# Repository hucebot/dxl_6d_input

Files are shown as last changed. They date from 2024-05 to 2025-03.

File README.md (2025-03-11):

# dxl_6d_input

[](
https://opensource.org/licenses/BSD-3-Clause)
[](
http://wiki.ros.org/noetic)

ROS package for a 6-d input device based on dynamixels.

The end effector of the device is a 6-DOF manipulator with 2 MX-64 and 5 MX-28 Dynamixels. The device is controlled by a ROS node that reads the position of the end effector and publishes it to a topic as also the position of the gripper. The node also subscribes to a topic to receive the actual position of the robot end effector to compensate the initial position of the device.

### Topics
#### Publishers
- `/dxl_6d_input/pos_{side}` - Publishes the position of the end effector.
- `/dxl_6d_input/gripper_{side}` - Publishes the position of the gripper.

#### Subscribers
- `/cartesian/gripper_{side}_grasping_frame/current_reference` - Subscribes to the position of the robot end effector.
- `/streamdeck/teleoperation_mode` - Subscribes to the teleoperation mode of the device.
- `/joy` - Subscribes to the joystick input.

### Parameters
- `~urdf_filename` - The URDF file of the device.
- `~ids` - The IDs of the Dynamixels.
- `~devicename` - The name of the port where the USB2Dynamixel is connected.
- `~baudrate` - The baudrate of the USB2Dynamixel.
- `~protocol_version` - The protocol version of the USB2Dynamixel.
- `~addr_present_position` - The address of the present position register.
- `~len_present_position` - The length of the present position register.
- `~debuginfo` - Flag to enable the debug information.
- `~arm_side` - The side of the arm.
- `~position_topic` - The topic where the position of the robot end effector is published.
- `~gripper_topic` - The topic where the position of the gripper is published.
- `~robot_position_topic` - The topic where the position of the robot end effector is subscribed.
- `~space_scalar` - The scalar to convert the position of the robot end effector to the device.

# Get Started

| 3D Design | 3D Design |
|---|---|
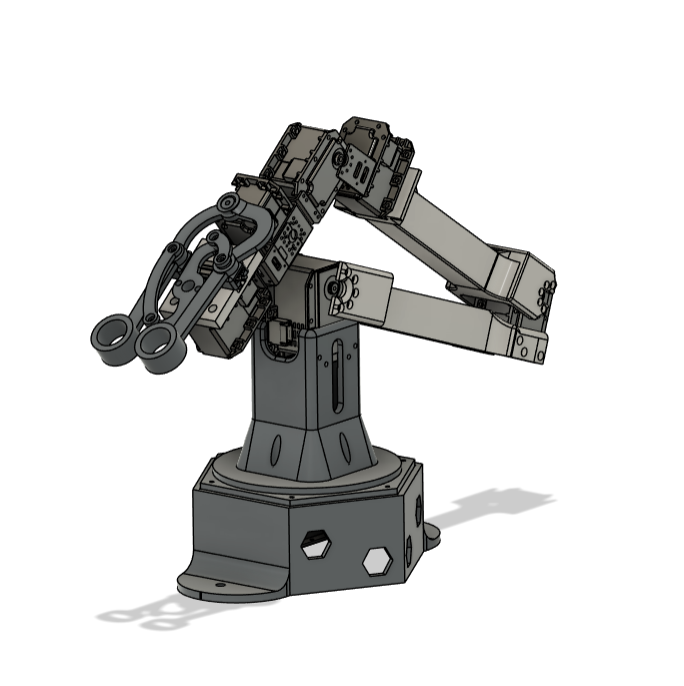
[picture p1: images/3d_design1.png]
3D Design
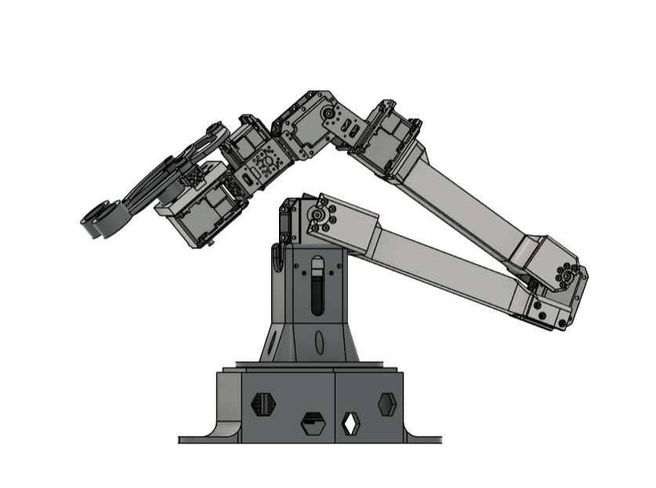
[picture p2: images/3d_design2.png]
3D Design
|  |  |

## Hardware
For the hardware setup, the package is designed to work with the 2 Dynamixel MX-64 and 5 Dynamixel MX-28 actuators. All the 3D parts can be found in the `dxl_6d_input/armd_design` folder where you will find the FreeCad files and the STL files for 3D printing. To assemble the device, you can follow the next steps:

### Shopping List
- 2 Dynamixel MX-64.
- 5 Dynamixel MX-28.
- 2 FR07 - H101K
- 4 FR07 - S101K
- Dynamixel cables.
- 1 USB2Dynamixel.
- 3D printed parts - PLA.
- Screws and nuts (M2, M3, M4, M5).
- 1 aluminum profile (10x10 mm) - 100 mm.

### Assembly
- Print the parts in the `dxl_6d_input/armd_design` folder. All the parts are designed to be printed with a **0.4mm nozzle and 0.2mm** layer height, with **40% infill** and **supports enabled** using **PLA**.
    - The files `finger_1.stl`, `finger_2.stl`, `griper_axis.stl`, `griper_axis_1.stl`, `griper_axis_1.stl` should be mirrored to print the left arm.
    - Once the parts are printed, you can start the assembly.
- The 2 Dynamixel MX-64 should be mounted on the base of the device, while the 5 Dynamixel MX-28 should be mounted on the arm.
- Be aware of the orientation of the Dynamixels:
    - First calibrate each motor to the zero position using the [Dynamixel Wizard2](https://emanual.robotis.com/docs/en/software/dynamixel/dynamixel_wizard2/).
    - Mount each motor following the joints directions. For a beter understanding of the joints, you can check the URDF file in the `dxl_6d_input/src` folder and view it with any URDF viewer.
- The aluminum profile should be mounted as a guide for the gripper. You can see it on the images above.
- We strongly **recommend to assemble from the bottom to the top.**
- For more information about the assembly, check [assembly instructions](https://github.com/hucebot/dxl_6d_input/blob/bimanual-teleoperation/assembly_guide.pdf)

## Installation

### From Docker

The easiest way to get started is to use the provided Docker image. You can find the Dockerfile in the `docker` folder. To build the image, run the following command:

```sh build.sh```

The run the command below to start the container (inside the `docker` folder):

```sh run_docker.sh```

# Usage

## Prepare the Dynamixels

Before starting the node, make sure that the Dynamixels are connected to the computer and that the USB2Dynamixel is connected to the computer. Also check the following:
- The protocol version is set to 2.0 for each Dynamixel.
- The baudrate is set to 1Mbps for each Dynamixel.
- The left arm it's connected to /dev/ttyUSB0 and the right arm to /dev/ttyUSB1.
- The Dynamixels are connected in the following order:

<center>

| Left Arm | Right Arm  |
| ------------- | ------------- |
| MX-64 - ID 1  | MX-64 - ID 11  |
| MX-64 - ID 2  | MX-64 - ID 12  |
| MX-28 - ID 3  | MX-28 - ID 13  |
| MX-28 - ID 4  | MX-28 - ID 14  |
| MX-28 - ID 5  | MX-28 - ID 15  |
| MX-28 - ID 6  | MX-28 - ID 16  |
| MX-28 - ID 7  | MX-28 - ID 17  |

</center>

## Start the Node

Once the Dynamixels are connected, you can start the node running the following command:

```roslaunch dxl_6d_input dxl_6d_input.launch```

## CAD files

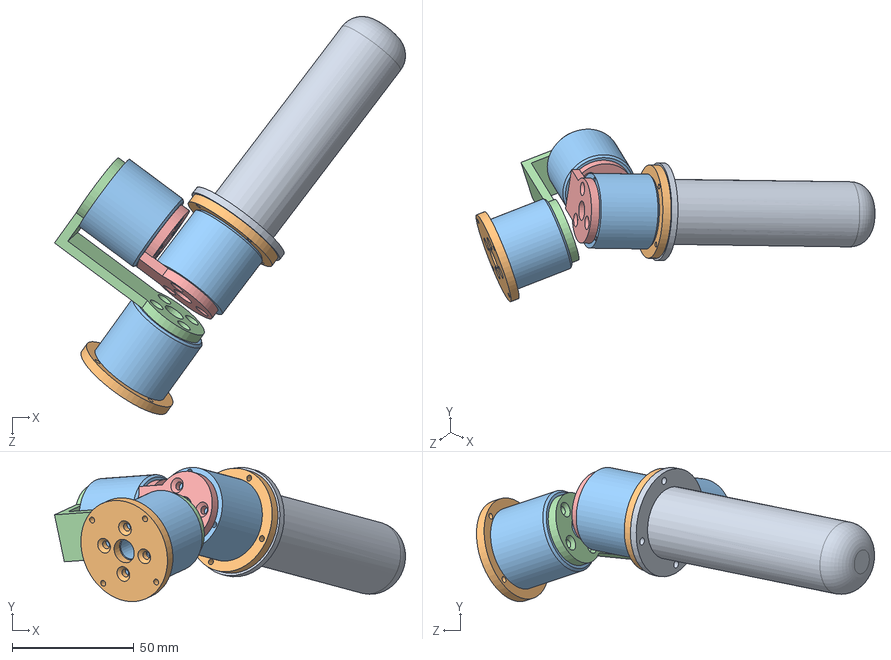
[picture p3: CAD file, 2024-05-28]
hardware/armAssembly.SLDASM
143.9 x 55.0 x 163.2 mm
handle
hub1 x 2
motorgl30 x 3
motorMount1
motorMount2

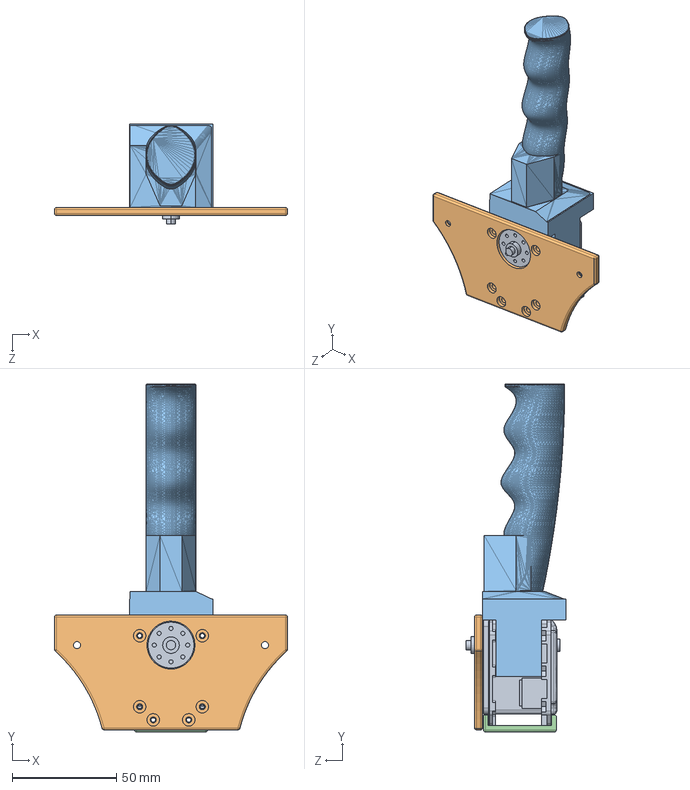
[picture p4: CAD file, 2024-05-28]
hardware/alohaRemixAsmb.SLDASM
111.6 x 166.6 x 48.1 mm
MX-28AT_AR.stp
motorHubDynamixel
handle_lower1_remix
handlerLinkDynamix1

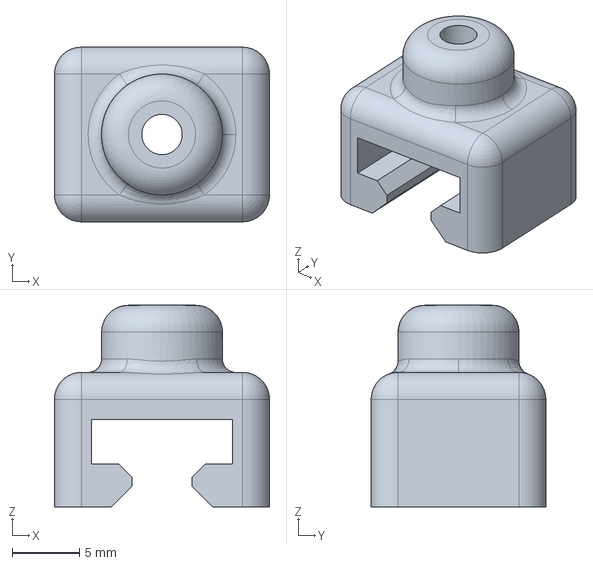
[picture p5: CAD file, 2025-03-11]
arm_design/auxiliar_guide.FCStd
16.0 x 13.0 x 15.0 mm

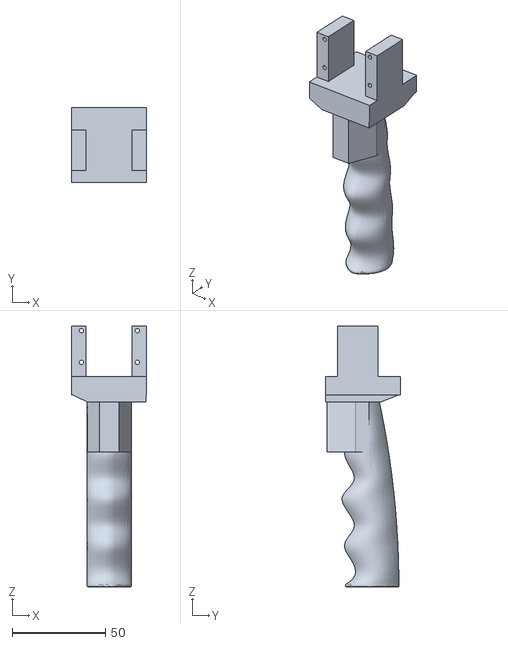
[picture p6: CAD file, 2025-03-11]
arm_design/stl_files/handle.stl
40.0 x 40.0 x 140.0

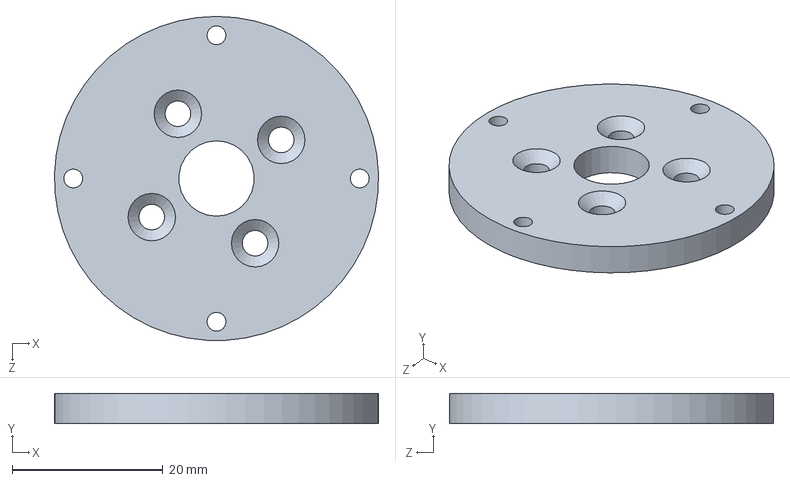
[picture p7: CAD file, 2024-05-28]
hardware/simpleGimball/hub1.SLDPRT
43.0 x 4.00 x 43.0 mm

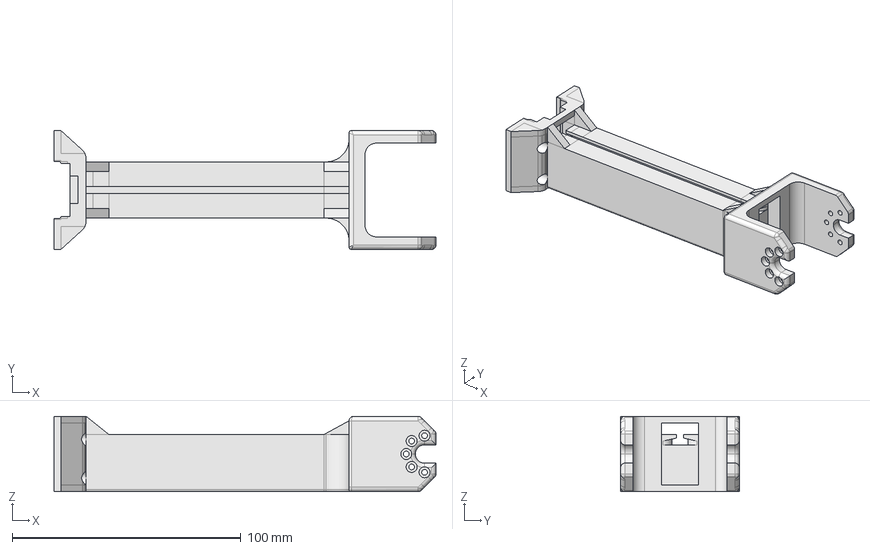
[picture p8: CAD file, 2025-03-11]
arm_design/arm_l2_fixed.FCStd
167.0 x 52.0 x 33.0 mm

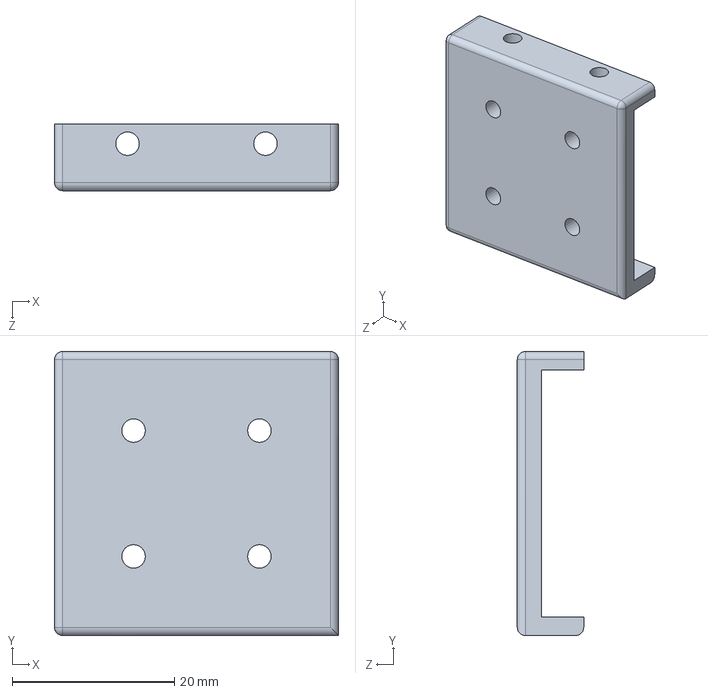
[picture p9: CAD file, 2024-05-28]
hardware/handlerLinkDynamix1.SLDPRT
35.0 x 35.0 x 8.20 mm

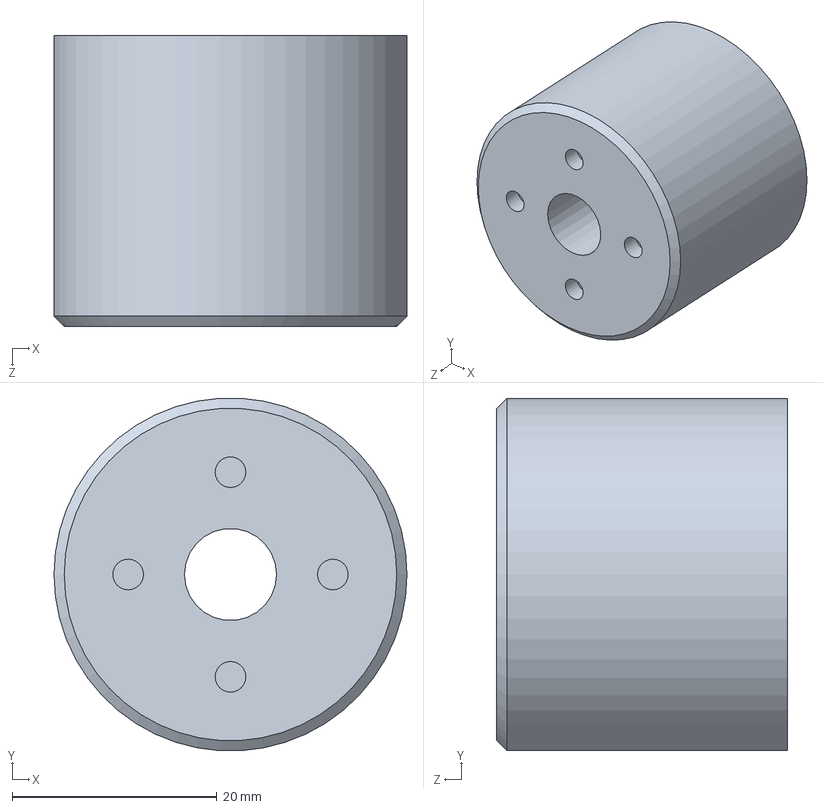
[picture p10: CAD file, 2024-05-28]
hardware/simpleGimball/motorgl30.SLDPRT
34.5 x 34.4 x 28.4 mm

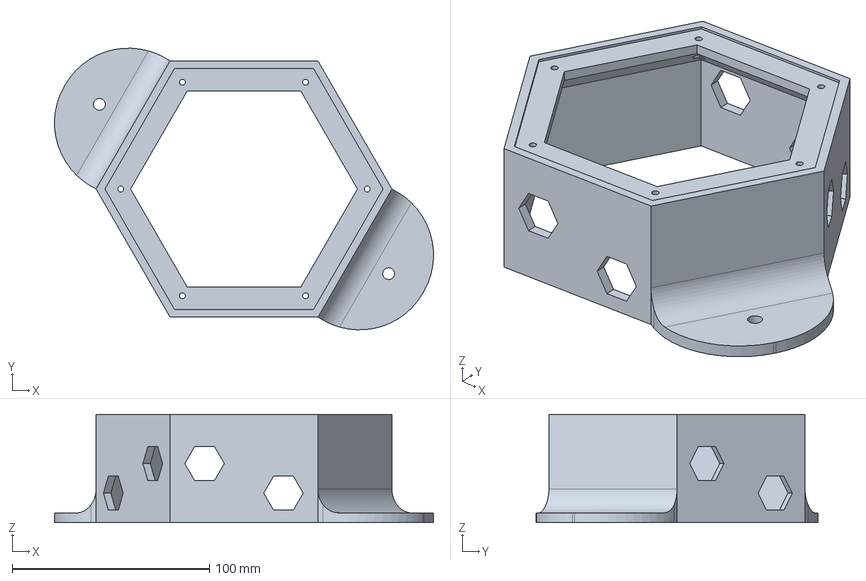
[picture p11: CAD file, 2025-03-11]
arm_design/base_1.FCStd
192.1 x 142.8 x 55.0 mm

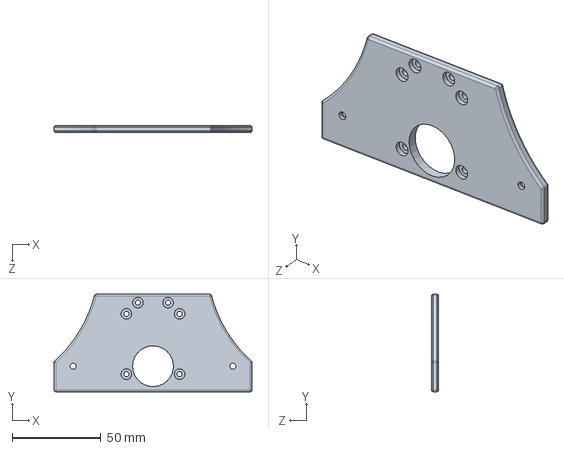
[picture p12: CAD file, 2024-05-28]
hardware/motorHubDynamixel.SLDPRT
111.6 x 55.0 x 4.00 mm

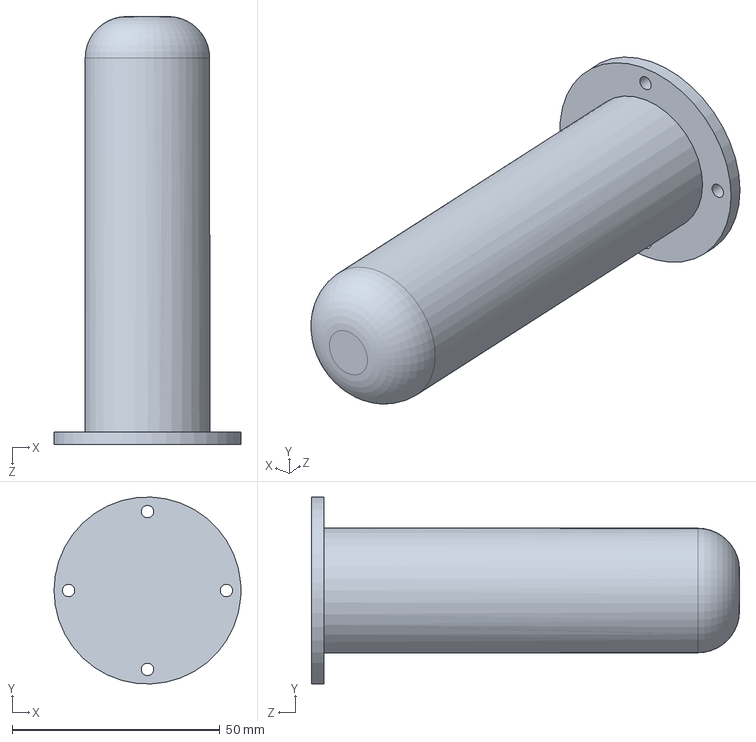
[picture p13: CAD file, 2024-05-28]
hardware/simpleGimball/handle.SLDPRT
45.0 x 45.0 x 103.0 mm

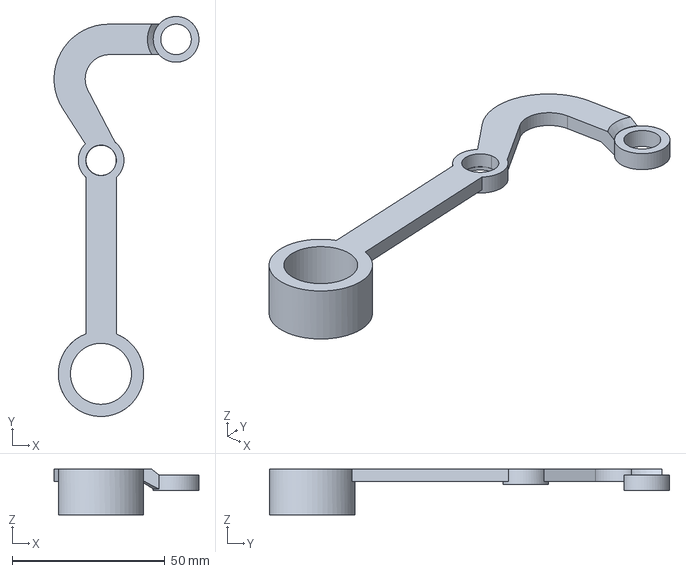
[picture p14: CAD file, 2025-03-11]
arm_design/finger_2.FCStd
47.5 x 131.2 x 15.0 mm

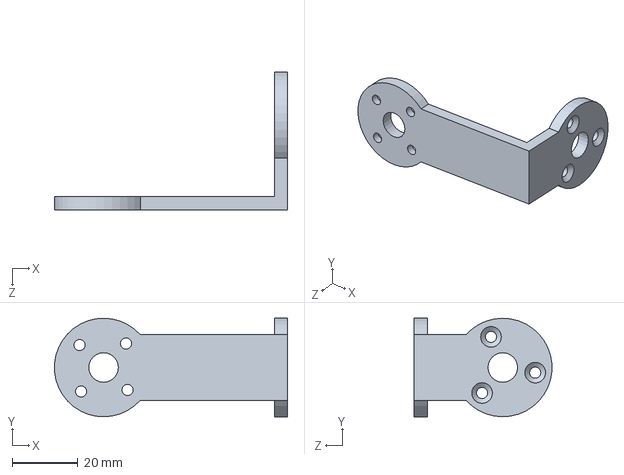
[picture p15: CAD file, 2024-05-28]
hardware/simpleGimball/motorMount1.SLDPRT
70.9 x 30.0 x 41.9 mm

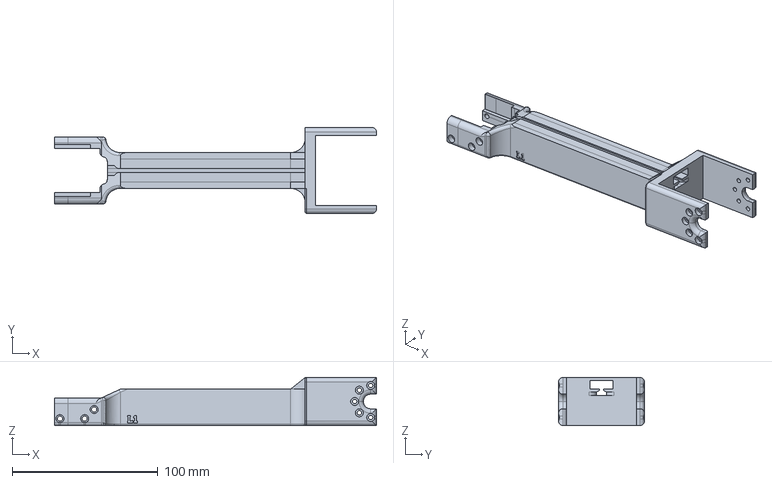
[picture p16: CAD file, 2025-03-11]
arm_design/arm_l1_fixed.FCStd
221.2 x 59.0 x 33.0 mm

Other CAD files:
hardware/simpleGimball/motorMount2.SLDPRT
arm_design/auxiliar_tape.FCStd
arm_design/base.FCStd
arm_design/gripper_motor_mount.FCStd
arm_design/base_0.FCStd
arm_design/base_plate.FCStd
arm_design/finger_1.FCStd
arm_design/gripper_axis.FCStd
arm_design/gripper_axis_1.FCStd
arm_design/gripper_axis_2.FCStd
arm_design/stl_files/arm_l1_fixed.stl
arm_design/stl_files/arm_l2_fixed.stl
arm_design/stl_files/auxiliar_guide.stl
arm_design/stl_files/auxiliar_tape.stl
arm_design/stl_files/base.stl
arm_design/stl_files/base_0.stl
arm_design/stl_files/base_1.stl
arm_design/stl_files/base_plate.stl
arm_design/stl_files/finger_1.stl
arm_design/stl_files/finger_2.stl
arm_design/stl_files/gripper_axis.stl
arm_design/stl_files/gripper_axis_1.stl
arm_design/stl_files/gripper_axis_2.stl
arm_design/stl_files/gripper_motor_mount.stl

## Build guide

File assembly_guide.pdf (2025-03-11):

# DXL 6D INPUT

# Assembly Guide

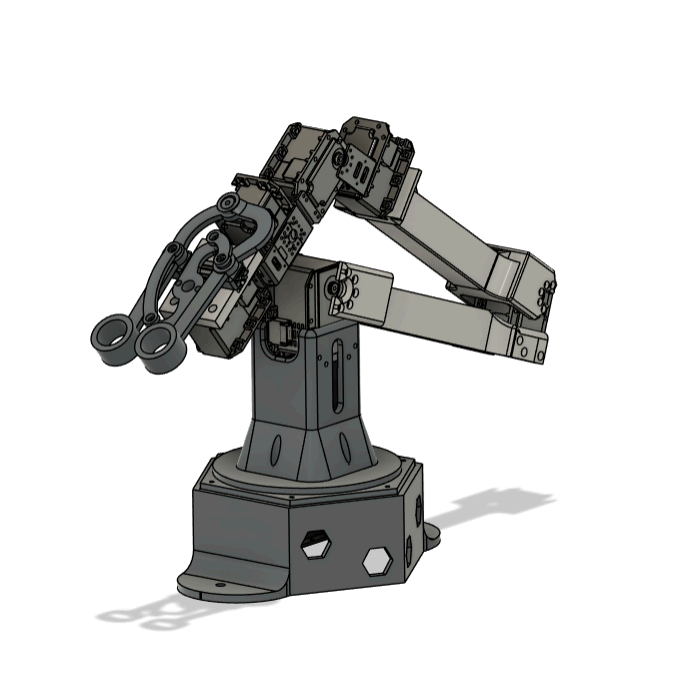
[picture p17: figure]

# Assembly Guide

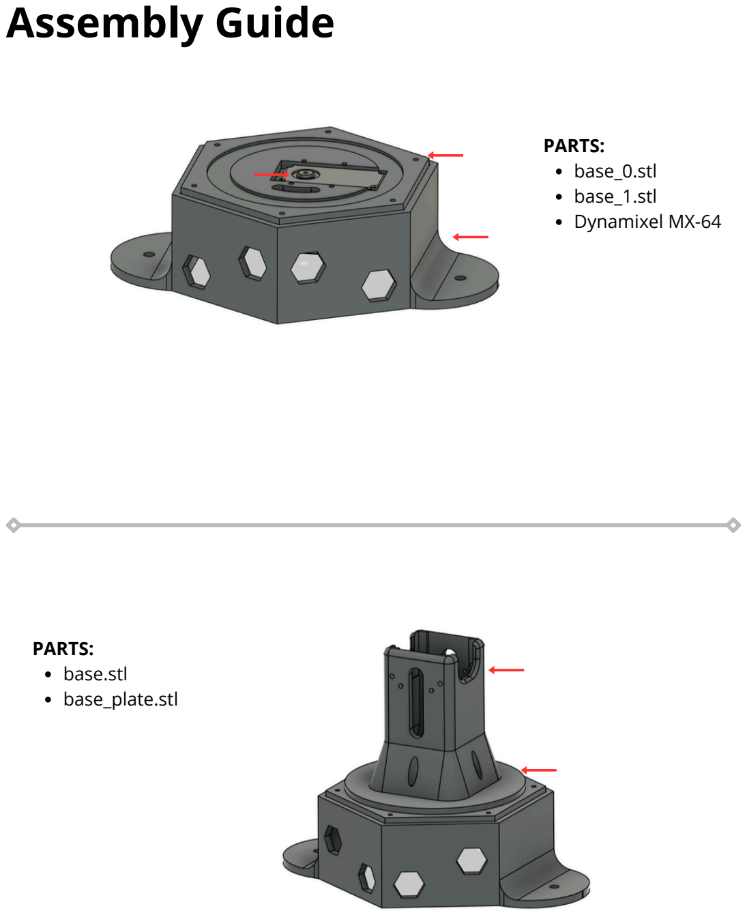
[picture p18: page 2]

PARTS:
base_0.stl
base_1.stl
Dynamixel MX-64

PARTS:
base.stl
base_plate.stl

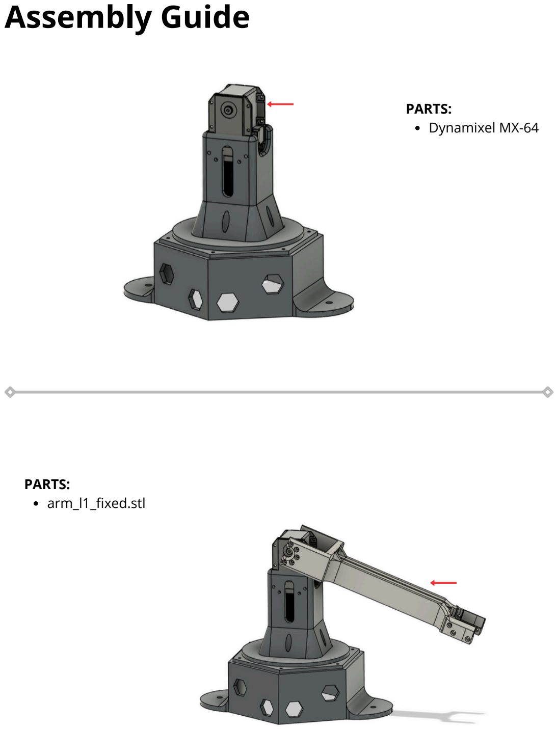
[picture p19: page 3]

PARTS:
Dynamixel MX-64

PARTS:
arm_l1_fixed.stl

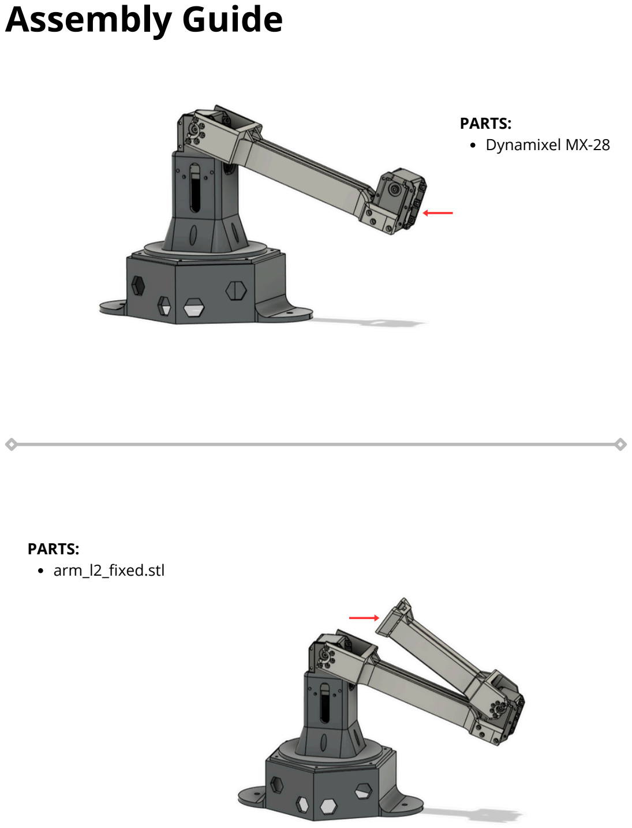
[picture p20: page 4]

PARTS:
Dynamixel MX-28

PARTS:
arm_l2_fixed.stl

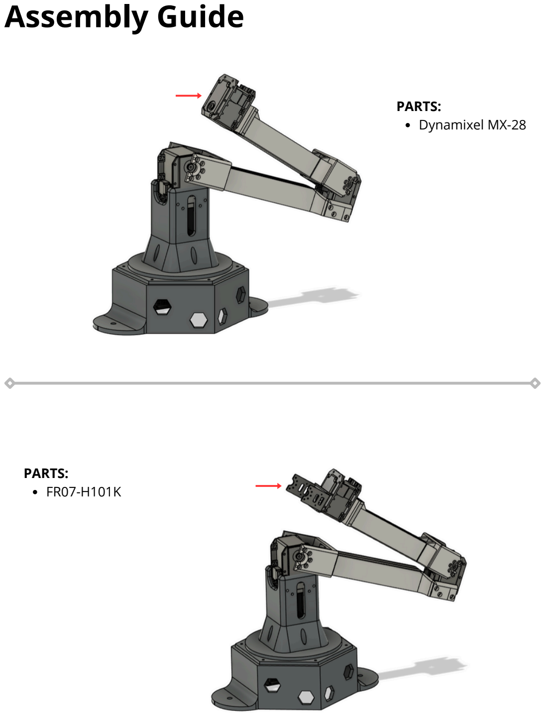
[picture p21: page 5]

PARTS:
Dynamixel MX-28

PARTS:
FR07-H101K

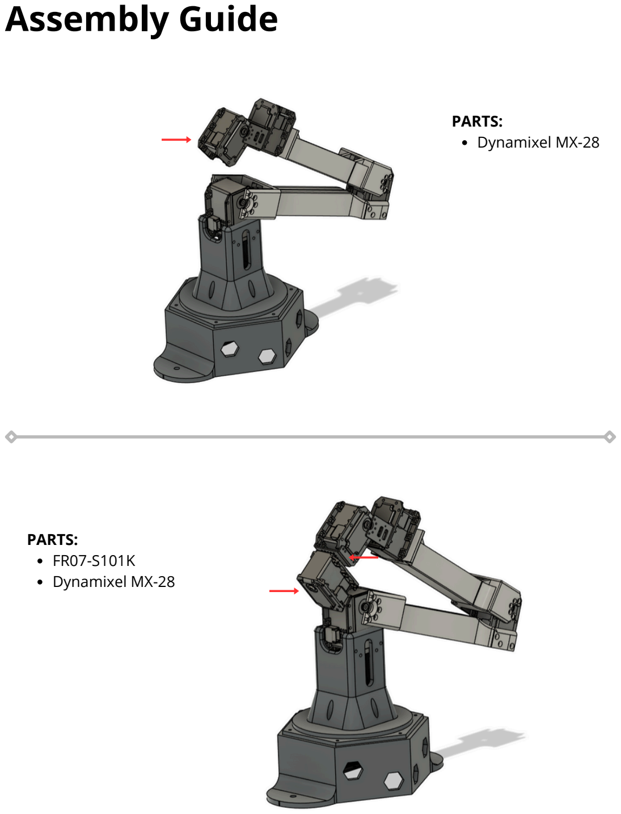
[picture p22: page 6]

PARTS:
Dynamixel MX-28

PARTS:
FR07-S101K
Dynamixel MX-28

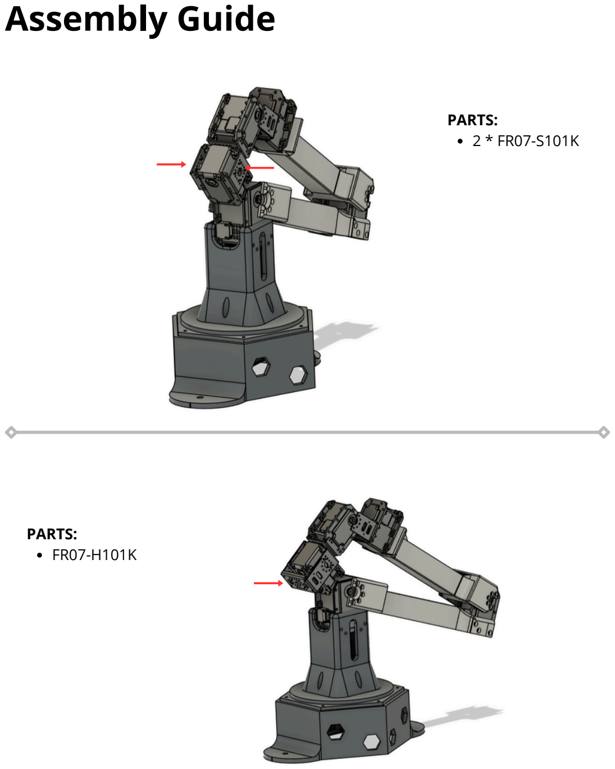
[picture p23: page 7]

PARTS:
2 * FR07-S101K

PARTS:
FR07-H101K

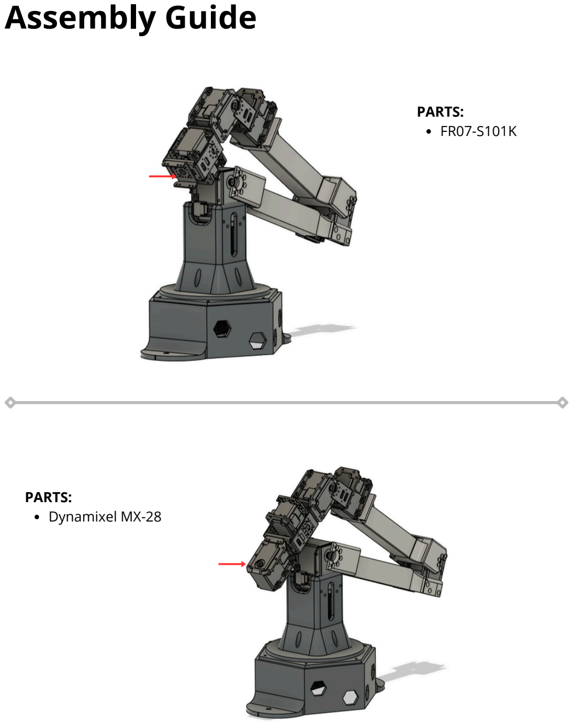
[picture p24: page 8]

PARTS:
FR07-S101K

PARTS:
Dynamixel MX-28

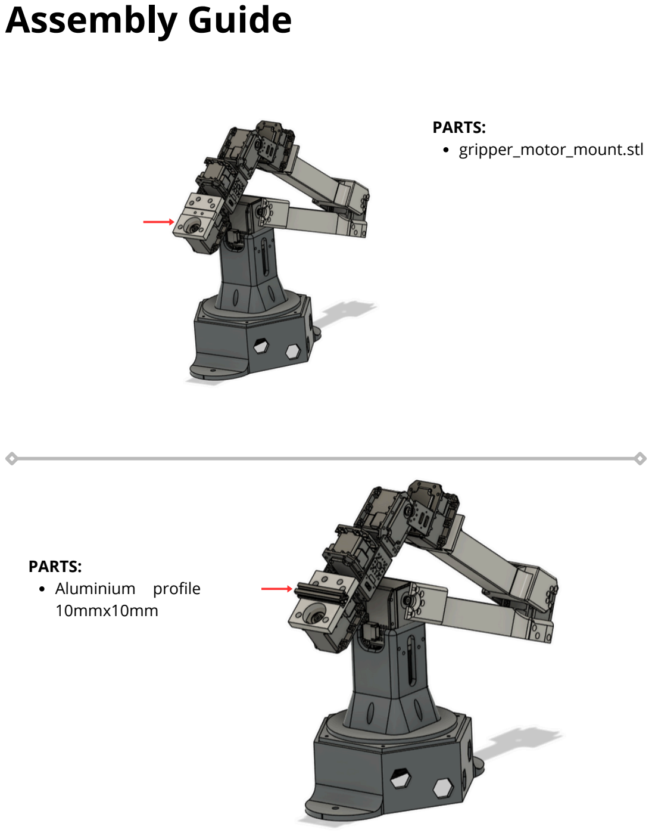
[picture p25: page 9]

PARTS:
gripper_motor_mount.stl

PARTS:
Aluminium profile
10mmx10mm

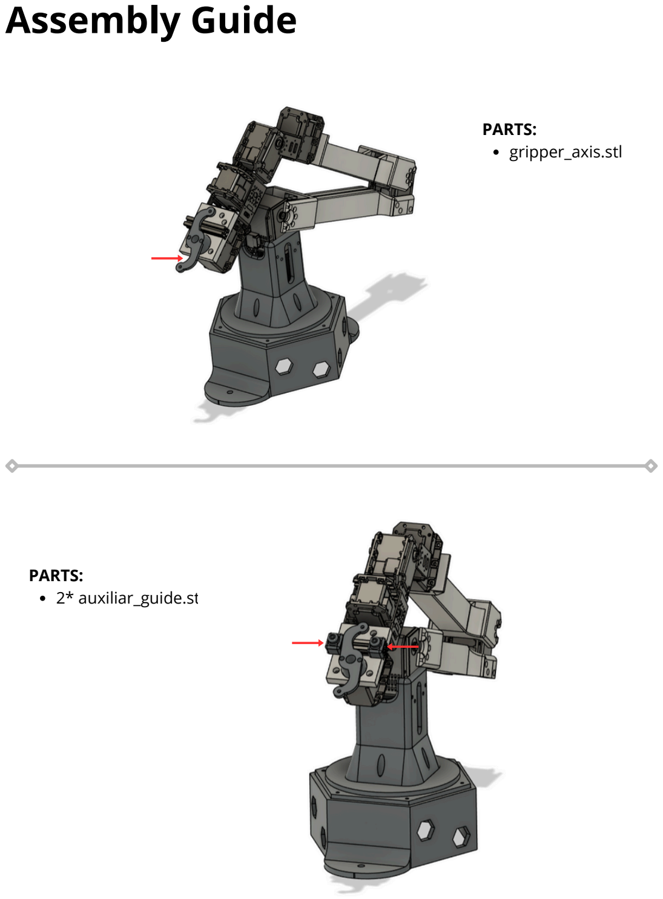
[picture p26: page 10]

PARTS:
gripper_axis.stl

PARTS:
2* auxiliar_guide.stl

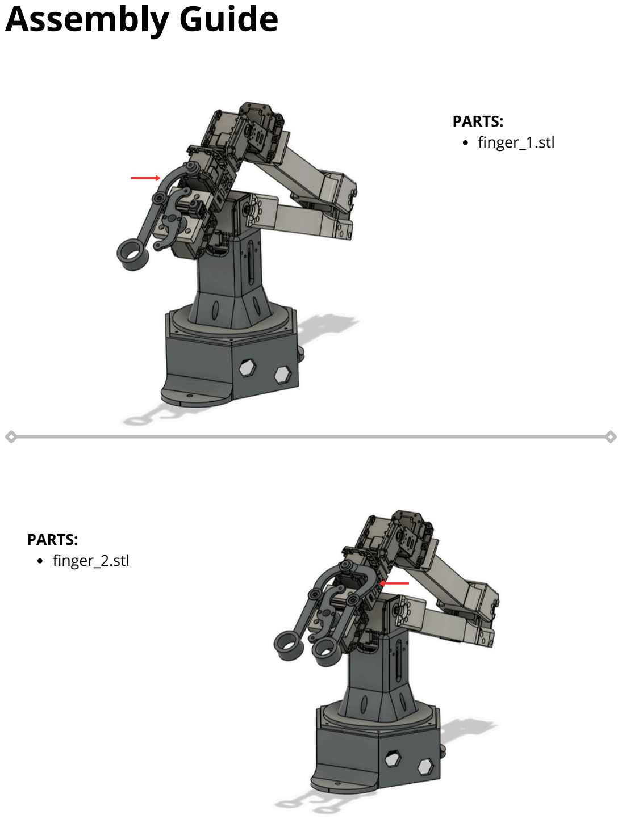
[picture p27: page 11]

PARTS:
finger_1.stl

PARTS:
finger_2.stl

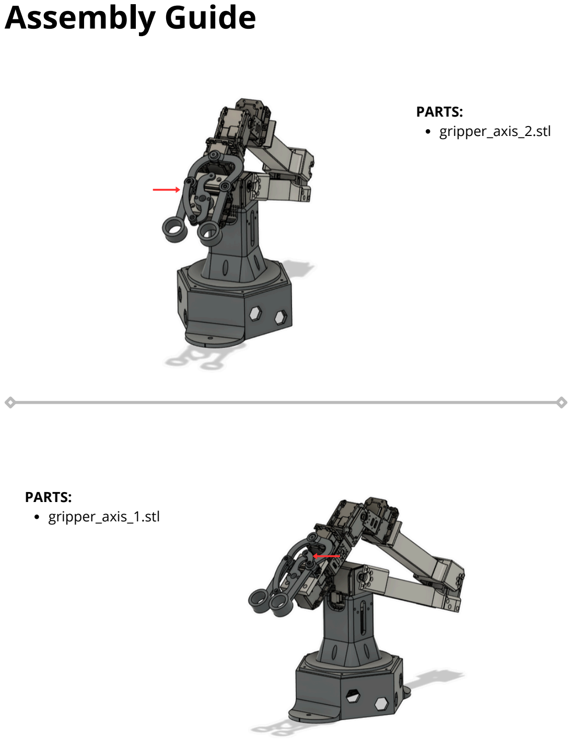
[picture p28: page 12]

PARTS:
gripper_axis_2.stl

PARTS:
gripper_axis_1.stl

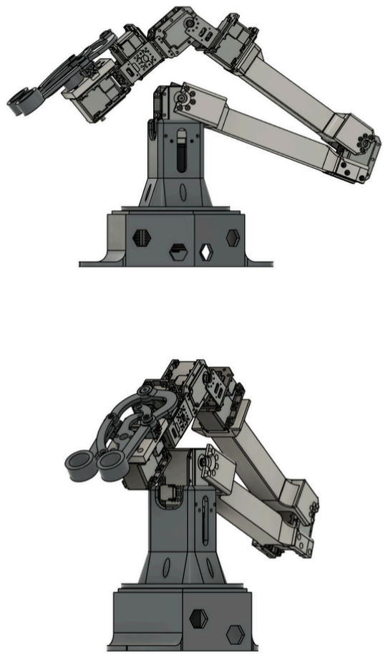
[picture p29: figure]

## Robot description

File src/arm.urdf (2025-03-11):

<?xml version="1.0"?>
<robot name="omnipointer">
  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
  <link name="base_link">
    <inertial>
      <origin rpy="0 0 0" xyz="0 0 0" />
      <mass value="10.0" />
      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
    </inertial>
  </link>
  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
  <joint name="arm_joint_0" type="fixed">
    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
    <origin rpy="0 0 0" xyz="0 0 0" />
    <parent link="base_link" />
    <child link="arm_link_0" />
  </joint>


  <link name="arm_link_0">
    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
    <inertial>
      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
      <origin rpy="0 0 0" xyz="0 0 0.03" />
      <mass value="0.2" />
      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
    </inertial>
  </link>


  <joint name="arm_joint_1" type="revolute">
    <parent link="arm_link_0" />
    <child link="arm_link_1" />
    <limit effort="5.0" lower="-3.1415926535" upper="3.1415926535" velocity="5.0" />
    <origin rpy="0 0 0.0" xyz="0 0 0.0600" />
    <axis xyz="0 0 1" />
    <dynamics damping="0.5" />
  </joint>


  <link name="arm_link_1">
    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

    <inertial>
      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
      <origin rpy="0 0 0" xyz="0 0 0.115" />
      <mass value="0.190421352" />
      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
    </inertial>
  </link>


  <joint name="arm_joint_2" type="revolute">
    <parent link="arm_link_1" />
    <child link="arm_link_2" />
    <limit effort="5.0" lower="-1.57079632679" upper="1.57079632679" velocity="5.0" />
    <origin rpy="0 0.0 0" xyz="0 0 0.115" />
    <axis xyz="0 1 0" />
    <dynamics damping="0.5" />
  </joint>


  <link name="arm_link_2">
    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
    <inertial>
      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
      <origin rpy="0 0 0" xyz="0 0 0.9375" />
      <mass value="0.29302326" />
      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
    </inertial>
  </link>


  <joint name="arm_joint_3" type="revolute">
    <parent link="arm_link_2" />
    <child link="arm_link_3" />
    <limit effort="5.0" lower="-1.57079632679" upper="1.57079632679" velocity="5.0" />
    <origin rpy="0 1.57 0" xyz="0.026 0 0.2050" />
    <axis xyz="0 1 0" />
    <dynamics damping="0.5" />
  </joint>


  <link name="arm_link_3">
    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
    <inertial>
      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
      <origin rpy="0 0 0" xyz="0 0 0.0825" />
      <mass value="0.21931466" />
      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
    </inertial>
  </link>

  <joint name="arm_joint_4" type="revolute">
    <parent link="arm_link_3" />
    <child link="arm_link_4" />
    <limit effort="5.0" lower="-1.57079632679" upper="1.57079632679" velocity="5.0" />
    <origin rpy="0 0 0.0" xyz="0 0 0.1975" />
    <axis xyz="0 0 1" />
    <dynamics damping="0.5" />
  </joint>


  <link name="arm_link_4">
    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
    <inertial>
      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
      <origin rpy="0 0 0" xyz="0 0 0.08025" />
      <mass value="0.15813986" />
      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
    </inertial>
  </link>

  <joint name="arm_joint_5" type="revolute">
    <parent link="arm_link_4" />
    <child link="arm_link_5" />
    <origin rpy="0 1.57 0" xyz="0 0 0.0425" />
    <axis xyz="0 1 0" />
    <limit effort="5.0" lower="-1.57079632679" upper="1.57079632679" velocity="5.0" />

  </joint>


  <link name="arm_link_5">
    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
    <inertial>
      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
      <origin rpy="0 0 0" xyz="0 0 0.08" />
      <mass value="0.15813986" />
      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
    </inertial>
  </link>


  <joint name="arm_joint_6" type="revolute">
    <parent link="arm_link_5" />
    <child link="arm_link_6" />
    <origin rpy="0 0 0.0" xyz="0 0 0.045" />
    <axis xyz="0 0 1" />
    <limit effort="5.0" lower="-1.57079632679" upper="1.57079632679" velocity="5.0" />

  </joint>


  <link name="arm_link_6">
    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
    <inertial>
      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
      <origin rpy="0 0 0" xyz="0 0 0.08025" />
      <mass value="0.15813986" />
      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
    </inertial>
  </link>


  <joint name="arm_joint_7" type="fixed">
    <parent link="arm_link_6" />
    <child link="tip" />
    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
    <origin rpy="3.1415 0. 3.1415" xyz="0 0 0.093"/>
    <axis xyz="0 1 0" />
  </joint>


  <link name="tip">
    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
    <inertial>
      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
      <origin rpy="0 0 0" xyz="0 0 0.08025" />
      <mass value="0.15813986" />
      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
    </inertial>
  </link>

  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
</robot>

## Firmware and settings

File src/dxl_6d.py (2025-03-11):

#!/usr/bin/env python3

from dynamixel_sdk import * 
import math
import time
import numpy as np
import pinocchio
import numpy as np
import rospy
from std_msgs.msg import Float64MultiArray, Float32, Bool
from sensor_msgs.msg import JointState, Joy
from geometry_msgs.msg import PoseStamped, PointStamped

class Dxl6d:
    def __init__(self):
        rospy.init_node('dxl_input', anonymous=True)
        rospy.loginfo("dxl_input node started")

        ###### ROS parameters
        self.urdf_filename = rospy.get_param('~urdf_filename', 'src/dxl_6d_input/src/arm.urdf')
        self.ids = rospy.get_param('~ids', [1,2,3,4,5,6,7])
        self.ids = self.ids.split(',') 
        self.ids = [int(i) for i in self.ids]
        self.devicename = rospy.get_param('~devicename', '/dev/ttyUSB0')
        self.baudrate = int(rospy.get_param('~baudrate', 1000000))
        self.protocol_version = float(rospy.get_param('~protocol_version', 2.0)) 
        self.addr_present_position = int(rospy.get_param('~addr_present_position', 132)) 
        self.len_present_position = int(rospy.get_param('~len_present_position', 4))
        self.debuginfo = bool(rospy.get_param('~debuginfo', False)) 
        self.arm_side = rospy.get_param('~arm_side', 'right') 
        self.position_topic = rospy.get_param('~position_topic', '/dxl_input/pos_right') 
        self.gripper_topic = rospy.get_param('~gripper_topic', '/dxl_input/gripper_right')
        self.robot_position_topic = rospy.get_param('~robot_position_topic', '/cartesian/gripper_right_grasping_frame/current_reference')
        self.space_scalar = float(rospy.get_param('~space_scalar', 2.0))
        self.rate_ = int(rospy.get_param('~rate', 100))

        # Dynamixel torque and position addresses
        self.torque_enable_addr = 64
        self.addr_goal_position = 116
        self.initial_position = []
        self.robot_position = []
        self.first_message = True
        self.initialized = False

        ###### Pinocchio for kinematics
        self.model = pinocchio.buildModelFromUrdf(self.urdf_filename)
        self.data = self.model.createData()
        self.motor_data = [None] * len(self.ids)
        self.frame_id = self.model.getFrameId("tip")
      
        ##### Dynamixel initialization
        self.portHandler = PortHandler(self.devicename)
        self.packetHandler = PacketHandler(self.protocol_version)
        if not self.portHandler.openPort():
            rospy.logerr("Failed to open the port")
            quit() 
        if not self.portHandler.setBaudRate(self.baudrate):
            rospy.logerr("Failed to change the baudrate")
            quit()

        self.groupSyncRead = GroupSyncRead(self.portHandler, self.packetHandler, self.addr_present_position, self.len_present_position)
        for i in self.ids:
            self.groupSyncRead.addParam(i)

        ###### ROS publishers and subscribers
        self.pub_pos = rospy.Publisher(self.position_topic, PoseStamped, queue_size=10) 
        self.pub_gripper = rospy.Publisher(self.gripper_topic, PointStamped, queue_size=10)
        self.robot_position = rospy.wait_for_message(self.robot_position_topic, PoseStamped, timeout=5).pose.position

        self.rate = rospy.Rate(self.rate_) 
        self.pose_msg = PoseStamped()
        self.gripper_msg = PointStamped()

    # Enable torque for all motors
    def enable_torque(self):
        self.is_torque_enabled = True
        try:
            for dxl_id in self.ids:
                dxl_comm_result, dxl_error = self.packetHandler.write1ByteTxRx(self.portHandler, dxl_id, self.torque_enable_addr, 1)
                if self.debuginfo:
                    if dxl_comm_result != COMM_SUCCESS:
                        rospy.logerr(f"Failed to enable torque for ID {dxl_id}: {self.packetHandler.getTxRxResult(dxl_comm_result)}")
                    elif dxl_error != 0:
                        rospy.logerr(f"Dynamixel error for ID {dxl_id}: {self.packetHandler.getRxPacketError(dxl_error)}")
                    else:
                        rospy.loginfo(f"Torque enabled for motor ID {dxl_id}")
        except Exception as e:
            rospy.logerr(f"Error enabling torque: {e}")

    # Disable torque for all motors
    def disable_torque(self):
        self.is_torque_enabled = False
        try:
            for dxl_id in self.ids:
                dxl_comm_result, dxl_error = self.packetHandler.write1ByteTxRx(self.portHandler, dxl_id, self.torque_enable_addr, 0)
                if self.debuginfo:
                    if dxl_comm_result != COMM_SUCCESS:
                        rospy.logerr(f"Failed to disable torque for ID {dxl_id}: {self.packetHandler.getTxRxResult(dxl_comm_result)}")
                    elif dxl_error != 0:
                        rospy.logerr(f"Dynamixel error for ID {dxl_id}: {self.packetHandler.getRxPacketError(dxl_error)}")
                    else:
                        rospy.loginfo(f"Torque disabled for motor ID {dxl_id}")
        except Exception as e:
            rospy.logerr(f"Error disabling torque: {e}")

    # Ping a motor (for future implementation)
    def ping(self, dxl_id):
        dxl_model_number, dxl_comm_result, dxl_error = self.packetHandler.ping(self.portHandler, dxl_id)
        if dxl_comm_result != COMM_SUCCESS:
            rospy.logerr(f"Failed to ping motor ID {dxl_id}: {self.packetHandler.getTxRxResult(dxl_comm_result)}")
        elif dxl_error != 0:
            rospy.logerr(f"Dynamixel error for ID {dxl_id}: {self.packetHandler.getRxPacketError(dxl_error)}")

    # Print debug information for the robot state
    def debug(self, debuginfo):
        if debuginfo:
            rospy.loginfo(("{:<24} : {: .3f} {: .3f} {: .3f} {: .2f}"
                    .format("tip", *self.data.oMf[self.frame_id].translation.T.flat , self.gripper_msg.x)))

    # Main loop to control the robot
    def loop(self):
        while not rospy.is_shutdown():
            try:
                dxl_comm_result = self.groupSyncRead.txRxPacket()
                if dxl_comm_result != COMM_SUCCESS and self.debuginfo:
                    rospy.logerr(f'groupSyncRead txRxPacket failed: {self.packetHandler.getTxRxResult(dxl_comm_result)}')

                # Get present position of each motor
                for i, id_ in enumerate(self.ids, start=1):
                    dxl_getdata_result = self.groupSyncRead.isAvailable(id_, self.addr_present_position, self.len_present_position)
                    if not dxl_getdata_result and self.debuginfo:
                        rospy.logerr(f"[ID:{i:03d}] groupSyncRead getdata failed")

                    present_position = self.groupSyncRead.getData(id_, self.addr_present_position, self.len_present_position)
                    self.motor_data[i - 1] = (present_position - 2048.) / 2048. * math.pi  # Convert encoder units to radians

                    # Apply inversion of direction for specific motors
                    if i == 5:
                        self.motor_data[i - 1] = -self.motor_data[i - 1]
                    
                    if i == 1 and id_ == 11:
                        self.motor_data[i - 1] -= math.pi

            except Exception as e:
                rospy.logerr(f"Error processing data from motors: {e}")

            # Forward kinematics and pose/gripper publishing (your existing code)
            q = np.array(self.motor_data[0:-1])  # Kinematic configuration excluding the gripper
            pinocchio.framesForwardKinematics(self.model, self.data, q)  # Forward kinematics
                # Get ID of the "tip" frame

            if self.initialized == False:
                self.initial_position = self.data.oMf[self.frame_id].translation.copy()
                self.initialized = True

            quat = pinocchio.Quaternion(self.data.oMf[self.frame_id].rotation)

            self.pose_msg.header.frame_id = "ci/world"
            self.pose_msg.pose.position.x = (self.data.oMf[self.frame_id].translation[0] - self.initial_position[0]) * self.space_scalar   + self.robot_position.x
            self.pose_msg.pose.position.y = (self.data.oMf[self.frame_id].translation[1] - self.initial_position[1]) * self.space_scalar  + self.robot_position.y
            self.pose_msg.pose.position.z = (self.data.oMf[self.frame_id].translation[2] - self.initial_position[2]) * self.space_scalar  + self.robot_position.z
            self.pose_msg.pose.orientation.x = quat.x
            self.pose_msg.pose.orientation.y = quat.y
            self.pose_msg.pose.orientation.z = quat.z
            self.pose_msg.pose.orientation.w = quat.w

            # Normalize the gripper data (open: -0.1135, closed: -0.3227)
            g = (self.motor_data[-1] + 0.1135) / (- 0.3227 + 0.1135)
            self.gripper_msg.point.x = 1 - np.clip(g, 0, 1)  # Clip between 0 and 1
            
            self.pose_msg.header.stamp = rospy.Time.now()
            self.gripper_msg.header = self.pose_msg.header
            self.pub_pos.publish(self.pose_msg)
            self.pub_gripper.publish(self.gripper_msg)

            self.rate.sleep()

        self.portHandler.closePort()

if __name__ == '__main__':
    node = Dxl6d()
    node.loop()

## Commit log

2024-04-24 add urdf
    [arm.urdf]
2024-05-14 improve urdf
    [arm.urdf]
2024-05-14 first prototype
    [arm.urdf]
2024-05-17 [hardware]: add CAD file of handle gimbal (simple version)
    [handle.SLDPRT, hub1.SLDPRT, motorMount1.SLDPRT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]
2024-05-21 [hardware] add arm assembly & gl30 motor model
    [armAssembly.SLDASM, motorgl30.SLDPRT]
2024-05-24 [hardware]: add remixed aloha gripper v1 to work with mx28-at
    [alohaRemixAsmb.SLDASM, handlerLinkDynamix1.SLDPRT, motorHubDynamixel.SLDPRT]
2024-05-28 version tested on tiago
    [arm.urdf]
2024-05-29 add the gripper
2024-05-30 gripper, less log
2024-09-12 Remove folder-specific mounting; use the container's internal structure
    - Eliminated the need to mount a specific host folder into the container
    - Configured the container to use its internal directory structure for builds
2024-09-12 Add launch file to run ROS scripts with custom parameters
    - Added parameters: `protocol_version`, `devicename`, `baudrate`, `addr_present_position`, `len_present_position`, `ids`, `urdf_filename`, and `debuginfo`
    - Simplified the execution of ROS scripts by centralizing parameter configuration in the launch file
    - Enables easy customization and debugging by adjusting parameters from the launch file
2024-09-16 Add Tiago bridge for teleoperation arm
    - Created `tiago_bridge` node based on `tiago_dual_cartesio_config`
    - Made minor adjustments to support teleoperation arm control
    - Ensured compatibility with the current teleoperation setup for seamless integration
2024-09-16 add launcher to control both arm
2024-09-16 Python script to be a bridge between the dxl script and control both arm with one control arm
2024-09-26 Correctly add IDs and configure launch files for teleoperation with both arms
    - Added correct IDs for each arm in the teleoperation setup
    - Updated launch files to support teleoperation with both left and right arms
    - Ensured proper communication and control for dual-arm operation
    - Tested and verified functionality for both arms simultaneously
    [dxl_6d.py]
2024-09-26 Add STL and FCStd files for arm design
    - Included STL files for 3D models of the arm components
    - Added FreeCAD (`.FCStd`) files for the full arm design
    - Organized files into appropriate directories for easy access and modification
    [arm_l1_fixed.stl, arm_l2_fixed.stl, auxiliar_guide.FCStd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]
2024-09-26 Update URDF with new dimensions, some elements still need adjustment
    - Modified URDF file to reflect the new dimensions of the arm components
    - Updated joint positions and link lengths according to the latest design
    - Some elements still require further adjustments for final accuracy
    [arm.urdf]
2024-09-27 Correct movement for the arms and urdf model
    [arm.urdf]
2024-09-27 FCStd and stl files for the arm
    [base.FCStd, base.stl, base_0.FCStd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]
2024-09-30 Update URDF and add arguments for each side of the arm
    - Updated URDF file to support the new configuration
    - Added arguments to handle left and right sides of the arm independently
    - Ensured compatibility with the teleoperation setup for dual-arm control
    [arm.urdf]
2024-09-30 Update code to use rospy logs instead of print statements
    - Replaced all `print` statements with appropriate `rospy.loginfo()`, `rospy.logwarn()`, and `rospy.logerr()` calls
    - Improved log readability and integration with ROS logging system
    - Removed unnecessary comments to clean up the code
    [dxl_6d.py]
2024-09-30 Update FCStd and STL files for the final version of the base
    - Updated FreeCAD (`.FCStd`) and STL files to reflect the final design of the arm's base
    - Refined dimensions and structure for improved stability and compatibility with the overall arm design
    [base_1.FCStd, base_1.stl, base_plate.FCStd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]
2024-10-01 Modify code to publish joint states and handle arm position translation
    - Implemented joint state publisher to broadcast current joint positions
    - Added functionality to translate the initial position of the arm and the current position
    - Ensured proper synchronization between initial and actual positions for accurate teleoperation
    - Improved feedback for better control and monitoring of the robot arm
    [arm.urdf]
2024-10-01 Minor changes to the arguments and also add topic to reset the position
    [dxl_6d.py]
2024-10-01 Add pedal control for sending commands to the robot and minor updates
    - Integrated pedal functionality to send commands to the robot, improving control flow
    - Both arms are now operational with synchronized movement
    - Made minor code adjustments and optimizations
    - Some issues remain to be fixed for full functionality and stability
    [dxl_6d.py]
2024-10-01 Add functionality to reset arm position using the pedal
    - Implemented a new feature that allows resetting the robot arm position via pedal input
    - Added logic to detect a specific pedal action and trigger the position reset
    [dxl_6d.py]
2024-10-02 Add streamdeck integration to enable teleoperation
    - Implemented streamdeck functionality to enable and control teleoperation
    - Added logic to toggle teleoperation mode using streamdeck buttons
2024-10-02 Update to enable the torque correctly
    [dxl_6d.py]
2024-10-02 Update the code to also take in count the robot position when reseting
    [dxl_6d.py]
2024-10-02 Updating the initialized to False while is reseting the position
    [dxl_6d.py]
2024-10-02 Enable the torque when you stop reseting the arm
    [dxl_6d.py]
2024-10-02 Change rate to 100 and also fix some issues with the torque
    [dxl_6d.py]
2024-10-02 Just send one time the enabled or disabled torque to the motor controller
2024-10-02 Minors update to move the arm without send the information to the robot
2024-10-02 Remove initial movement tests and clean up code
    - Deleted initial movement test logic to prevent unnecessary actions at startup
    - Cleaned up the code for better readability and maintainability
    - Retained functionality for controlling the arm lock/unlock solely through the pedal
    - Ensured the system operates with the pedal-based locking mechanism for both arms
    [dxl_6d.py]
2024-10-03 Add Kalman filter for smoother movements (needs testing)
    - Integrated a Kalman filter to reduce noise and provide smoother robot movements
    - Initial implementation is functional but requires further testing and fine-tuning
    [dxl_6d.py]
2024-10-04 Fix bugs and adjust logic for pedal control
    - Corrected various errors and bugs in the code
    - Modified the control logic to improve pedal functionality
    - Integrated position reset feature with pedal input, now working correctly
    [dxl_6d.py]

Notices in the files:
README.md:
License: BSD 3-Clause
